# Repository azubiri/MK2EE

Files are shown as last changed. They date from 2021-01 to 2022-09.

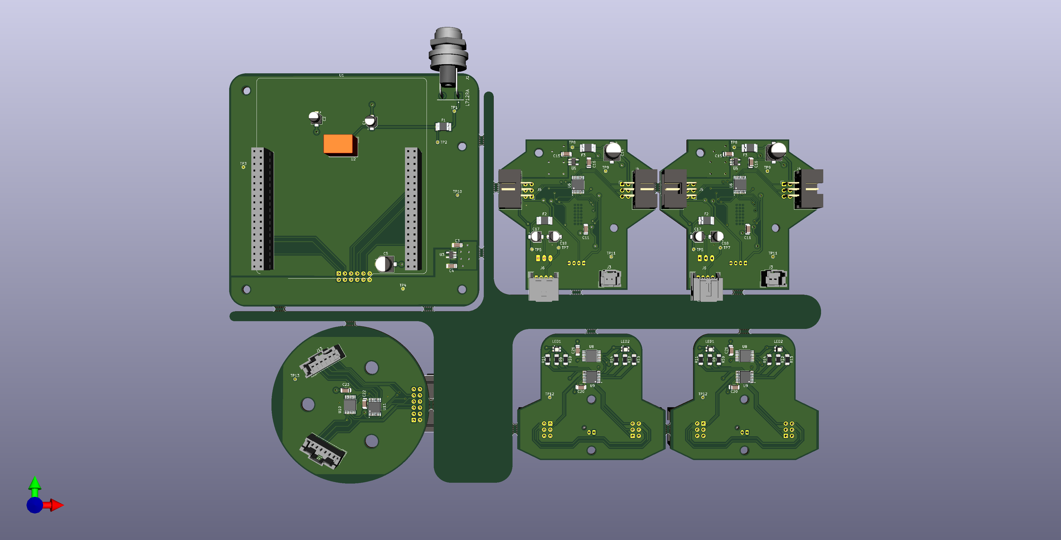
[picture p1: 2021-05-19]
mk2ee_kicad_project/Virtual_Images/PCBs_Manufactured_with_comp_front.png

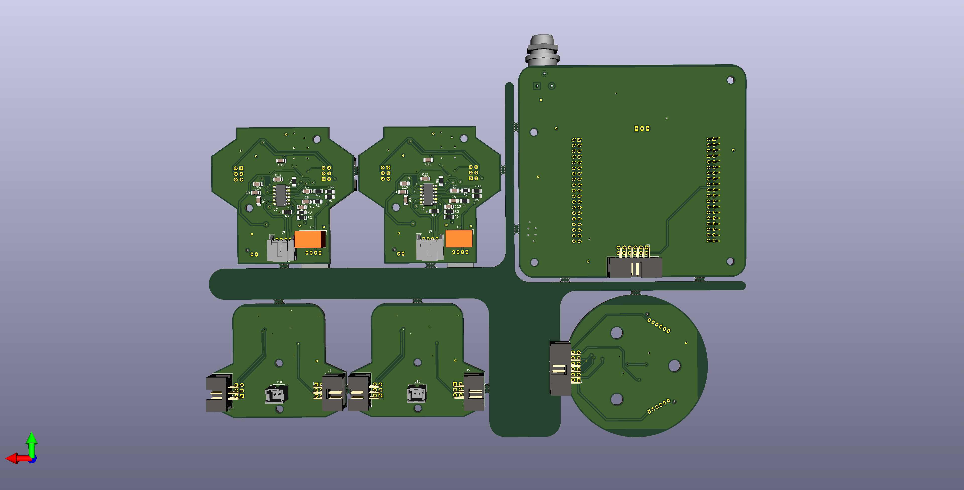
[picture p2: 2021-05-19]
mk2ee_kicad_project/Virtual_Images/PCBs_Manufactured_with_comp_back.png

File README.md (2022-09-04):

# MK2EE
## Introduction
The main goal of this project is a fabrication of robotic arm. This project is based on a previous project that is called [MK2Plus](https://www.instructables.com/Robot-Arm-MK2-Plus-Stepper-Motor-Used/). This previous project is a purpose which the joints of the robot are moved by stepper motors instead of servo motors like another project [EEZYbotARM MK2](http://www.eezyrobots.it/eba_mk2.html).

These additions which are implemented in this project are the following:
* Rotatory information of the joints that are provided by magnetic encoders.
* All electronic is integrated in the robot.
* Stressfuls for cables are avoided.

In this repository you will find the several files to replicate and improve this purposed robotic arm. It is structured by the mechanical part, electronic part and software that have been used to test the electronic part. In addition, there is anohter folder where you will find some software tools.

This project was a part of Master's Thesis. You can see more details about it in the documentation folder.

## Software requirements
### Mechanical part
* Autodesk Fusion 360 (recommended)
* FreeCAD (optional)
### Electronic part
* KiCad
### Software testing
* Visual Studio Code with PlatformIO extension (recommended)
* Mbed OS (optional)
### Software utilities
* Jupyter Notebook

## ToDo list
### Mechanical Part
- [ ] Paste one of the gear that is coupled with a stepper motor.
- [ ] Make a new gripper using a microservo and energised with 5V.

### Electronical Part
- [ ] Solder 2 EncoderPCB
- [ ] Solder 2 DriverPCB
- [ ] Solder 1 EncoderPCB2
- [ ] Solder 1 SupplyPCB

(see some important information in the README file inside mk2ee_kicad_project)

### Firmware Part
- [x] Test EncoderPCB with a Nucleo Board F303RE
- [x] Test DriverPCB with a Nucleo Board F303RE
- [x] Test EncoderPCB with a Nucleo Board F411RE
- [x] Test DriverPCB with a Nucleo Board F411RE
- [ ] Test EncoderPCB2 with a Nucleo Board F411RE
- [ ] Final testing SupplyPCB + EncoderPCB2 + 3xEncoderPCB + 3xDriverPCB

(see more details in the README file inside mk2ee_software_testing folder)

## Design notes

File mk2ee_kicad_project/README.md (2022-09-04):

# Electronical part
You can use these files to modify the circuits and PCBs with Kicad.

## Reworkings
- The linear regulator that is used in the DriverPCB design, is not found in the market. You can use other regulators with the same case style, but the function of each pin is different.
- The pads of the RGB leds in EncoderPCB. Pin 1 has to be put as cathode, and the rest (2, 3 and 4) as anode.

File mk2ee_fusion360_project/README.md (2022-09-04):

# Mechanical part
If you just want print the different parts of the robot, you can use directly the STL files.
But if you want to make modifications, you have to use the .f3z file using Fusion 360 software.

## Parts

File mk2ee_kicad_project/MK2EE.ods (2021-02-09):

Individual Components:
 |  | Reference(s) | Value | LibPart | Footprint | Manufacturer | Name
 |  | C1 | 10uF | Device:CP1 | Capacitor_SMD:CP_Elec_4x5.4 | Panasonic | EEEFK1E100R
 |  | C2 | 10uF | Device:CP1 | Capacitor_SMD:CP_Elec_4x5.4 | Kemet | EDK106M063A9GAA
 |  | C3 | 1uF | Device:C | Capacitor_SMD:C_1206_3216Metric | MULTICOMP PRO | MC1206B102K500CT
 |  | C4 | 1uF | Device:C | Capacitor_SMD:C_1206_3216Metric | MULTICOMP PRO | MC1206B102K500CT
 |  | C5 | 100uF | Device:CP1 | Capacitor_SMD:CP_Elec_6.3x7.7 | Panasonic | EEEFK1E101XP
 |  | C6 | 1000pF | Device:C | Capacitor_SMD:C_1206_3216Metric | MULTICOMP PRO | MC1206B102K500CT
 |  | C7 | 1000pF | Device:C | Capacitor_SMD:C_0805_2012Metric_Pad1.15x1.40mm_HandSolder | MULTICOMP PRO | MC1206B102K500CT
 |  | C8 | 0.22uF | Device:C | Capacitor_SMD:C_1206_3216Metric | Kemet | C1206C224K5RACTU
 |  | C9 | 0.22uF | Device:C | Capacitor_SMD:C_1206_3216Metric | Kemet | C1206C224K5RACTU
 |  | C10 | 0.22uF | Device:C | Capacitor_SMD:C_1206_3216Metric | Kemet | C1206C224K5RACTU
 |  | C11 | 100nF | Device:C | Capacitor_SMD:C_1206_3216Metric | Kemet | C1206C104K5RACTU
 |  | C12 | 100nF | Device:C | Capacitor_SMD:C_1206_3216Metric | Kemet | C1206C104K5RACTU
 |  | C13 | 100nF | Device:C | Capacitor_SMD:C_1206_3216Metric | Kemet | C1206C104K5RACTU
 |  | C14 | 100uF | Device:CP1 | Capacitor_SMD:CP_Elec_6.3x7.7 | Panasonic | EEEFK1E101XP
 |  | C15 | 1uF | Device:C | Capacitor_SMD:C_1206_3216Metric
 |  | C16 | 1uF | Device:C | Capacitor_SMD:C_1206_3216Metric
 |  | C17 | 10uF | Device:CP1 | Capacitor_SMD:CP_Elec_4x5.4 | Panasonic | EEEFK1E100R
 |  | C18 | 10uF | Device:CP1 | Capacitor_SMD:CP_Elec_4x5.4 | Panasonic | EEEFK1E100R
 |  | C19 | 100nF | Device:C | Capacitor_SMD:C_1206_3216Metric | Kemet | C1206C104K5RACTU
 |  | C20 | 100nF | Device:C
 |  | C21 | 100nF | Device:CP1 | Capacitor_SMD:CP_Elec_6.3x7.7 | Kemet | EDK106M063A9GAA
 |  | C22 | 100nF | Device:C
 |  | C23 | 100nF | Device:C
 |  | F1 | Polyfuse | MINISMDC110F_16-2:MINISMDC110F_16-2 | MK2Library:MINISMDC110 | Littlefuse | MINISMDC110F/24-2
 |  | F2 | Polyfuse | MINISMDC110F_16-2:MINISMDC110F_16-2 | MK2Library:MINISMDC110 | Littlefuse | MINISMDC110F/24-2
 |  | F3 | Polyfuse | MINISMDC110F_16-2:MINISMDC110F_16-2 | MK2Library:MINISMDC110 | Littlefuse | MINISMDC110F/24-2
 |  | J1 | L712RA | Switchcraft_-_L712RA:L712RA | MK2Library:Switchcraft-L712RA-0 | Switchcraft | L712RAS
 |  | J2 | Conn_02x6_Male | Connector:Conn_01x12_Male | Connector_PinSocket_2.54mm:PinSocket_2x06_P2.54mm_Horizontal | AMPHENOL ICC | T821112A1R100CEU
 |  | J3 | Conn_01x02_Male | Connector:Conn_01x02_Male | MK2Library:Molex_MicroClasp_55932-0210_1x02_P2.00mm_Vertical | Molex | 55932-0210
 |  | J4 | Conn_02x03_Male | Connector:Conn_01x06_Male | Connector_IDC:IDC-Header_2x03_P2.54mm_Horizontal | AMPHENOL ICC | T821106A1R100CEU
 |  | J5 | Conn_02x03_Male | Connector:Conn_01x06_Male | Connector_IDC:IDC-Header_2x03_P2.54mm_Horizontal | AMPHENOL ICC | T821106A1R100CEU
 |  | J6 | Conn_01x04_Male | Connector:Conn_01x04_Male | MK2Library:Molex_MicroClasp_55935-0430_1x04_P2.00mm_Horizontal | Molex | 502443-0470
 |  | J7 | Conn_01x04_Male | Connector:Conn_01x04_Male | MK2Library:Molex_MicroClasp_55935-0430_1x04_P2.00mm_Horizontal | Molex | 502443-0470
 |  | J8 | Conn_02x03_Male | Connector:Conn_01x06_Male | Connector_IDC:IDC-Header_2x03_P2.54mm_Horizontal | AMPHENOL ICC | T821106A1R100CEU
 |  | J9 | Conn_02x03_Male | Connector:Conn_01x06_Male | Connector_IDC:IDC-Header_2x03_P2.54mm_Horizontal | AMPHENOL ICC | T821106A1R100CEU
 |  | J10 | Conn_01x02_Male | Connector:Conn_01x02_Male | MK2Library:Molex_MicroClasp_55932-0210_1x02_P2.00mm_Vertical | Molex | 55932-0210
 |  | J11 | Conn_02x6_Male | Connector:Conn_01x12_Male | Connector_PinSocket_2.54mm:PinSocket_2x06_P2.54mm_Horizontal | AMPHENOL ICC | T821112A1R100CEU
 |  | J12 | Conn_02x03_Male | Connector:Conn_01x06_Male | MK2Library:901303206 | Molex | 90130-3206
 |  | J13 | Conn_02x03_Male | Connector:Conn_01x06_Male | MK2Library:901303206 | Molex | 90130-3206
 |  | LED1 | ASMB-KTF0-0A306 | ASMB-KTF0-0A306:ASMB-KTF0-0A306 | MK2Library:ASMBKTF00A306 | Avago Technologies | ASMB-KTF0-0A306
 |  | LED2 | ASMB-KTF0-0A306 | ASMB-KTF0-0A306:ASMB-KTF0-0A306 | MK2Library:ASMBKTF00A306 | Avago Technologies | ASMB-KTF0-0A306
 |  | R1 | 47k | Device:R | Resistor_SMD:R_1206_3216Metric | MULTICOMP PRO | MCWR12X4702FTL
 |  | R2 | 10k | Device:R | Resistor_SMD:R_0805_2012Metric_Pad1.15x1.40mm_HandSolder | MULTICOMP PRO | MC0125W1206510K
 |  | R3 | 10k | Device:R | Resistor_SMD:R_0805_2012Metric_Pad1.15x1.40mm_HandSolder | MULTICOMP PRO | MC0125W1206510K
 |  | R4 | 10k | Device:R | Resistor_SMD:R_0805_2012Metric_Pad1.15x1.40mm_HandSolder | MULTICOMP PRO | MC0125W1206510K
 |  | R5 | 10k | Device:R | Resistor_SMD:R_0805_2012Metric_Pad1.15x1.40mm_HandSolder | MULTICOMP PRO | MC0125W1206510K
 |  | R6 | 47k | Device:R | Resistor_SMD:R_1206_3216Metric | MULTICOMP PRO | MCWR12X4702FTL
 |  | R7 | 0.43R | Device:R | Resistor_SMD:R_1206_3216Metric | BOURNS | CRL1206-FW-R430ELF
 |  | R8 | 0.43R | Device:R | Resistor_SMD:R_0805_2012Metric_Pad1.15x1.40mm_HandSolder | BOURNS | CRL1206-FW-R430ELF
 |  | R9 | 82 | Device:R | Resistor_SMD:R_1206_3216Metric | MULTICOMP PRO | MCWR12X82R0FTL
 |  | R10 | 100 | Device:R | Resistor_SMD:R_1206_3216Metric | MULTICOMP PRO | MCWR12X1000FTL
 |  | R11 | 270 | Device:R | Resistor_SMD:R_1206_3216Metric | MULTICOMP PRO | MCWR12X2700FTL
 |  | R12 | 82 | Device:R | Resistor_SMD:R_1206_3216Metric | MULTICOMP PRO | MCWR12X82R0FTL
 |  | R13 | 100 | Device:R | Resistor_SMD:R_1206_3216Metric | MULTICOMP PRO | MCWR12X1000FTL
 |  | R14 | 270 | Device:R | Resistor_SMD:R_1206_3216Metric | MULTICOMP PRO | MCWR12X2700FTL
 |  | U1 | NUCLEO-F411RE | NUCLEO-F411RE:NUCLEO-F401RE | MK2Library:ST_NUCLEO-F401RE | STMicroelectronics | Nucleo-F411RE
 |  | U2 | TSR_1-24150 | Regulator_Switching:TSR_1-24150 | Converter_DCDC:Converter_DCDC_TRACO_TSR-1_THT | Traco Power | TSR 1-2450
 |  | U3 | NCP718xSN330 | Regulator_Linear:NCP718xSN330 | Package_TO_SOT_SMD:SOT-23-5 | ON SEMICONDUCTOR | NCP718BSN330T1G
 |  | U4 | TSR_1-2465 | Regulator_Switching:TSR_1-2465 | Converter_DCDC:Converter_DCDC_TRACO_TSR-1_THT | Traco Power | TSR 2-2465
 |  | U5 | NCP718xSN330 | Regulator_Linear:NCP718xSN330 | Package_TO_SOT_SMD:SOT-23-5
 |  | U6 | 74HC595 | 74xx:74HC595 | MK2Library:SN74HC595PWR | Texas Instruments | SN74HC595PWR
 |  | U7 | DRV8818PWP | DRV8818PWP:DRV8818PWP | MK2Library:DRV8818PWP | Texas Instruments | DRV8818PWR
 |  | U8 | AS5047D-ATSM | AS5047D-ATSM:AS5047D-ATSM | MK2Library:AS5047D-ATSM | ams | AS5047D-ATSM
 |  | U9 | 74HC595 | 74xx:74HC595 | MK2Library:SN74HC595PWR | Texas Instruments | SN74HC595PWR
 |  | U10 | AS5047D-ATSM | AS5047D-ATSM:AS5047D-ATSM | MK2Library:AS5047D-ATSM | ams | AS5047D-ATSM
 |  | U11 | 74HC595 | 74xx:74HC595 | MK2Library:SN74HC595PWR | Texas Instruments | SN74HC595PWR
Collated Components:
Item | Qty | Reference(s) | Value | LibPart | Footprint | Manufacturer | Name
1 | 4 | C1, C2, C17, C18 | 10uF | Device:CP1 | Capacitor_SMD:CP_Elec_4x5.4 | Panasonic | EEEFK1E100R
2 | 4 | C3, C4, C15, C16 | 1uF | Device:C | Capacitor_SMD:C_1206_3216Metric | MULTICOMP PRO | MC1206B102K500CT
3 | 2 | C5, C14 | 100uF | Device:CP1 | Capacitor_SMD:CP_Elec_6.3x7.7 | Panasonic | EEEFK1E101XP
4 | 1 | C6 | 1000pF | Device:C | Capacitor_SMD:C_1206_3216Metric | MULTICOMP PRO | MC1206B102K500CT
5 | 1 | C7 | 1000pF | Device:C | Capacitor_SMD:C_0805_2012Metric_Pad1.15x1.40mm_HandSolder | MULTICOMP PRO | MC1206B102K500CT
6 | 3 | C8, C9, C10 | 0.22uF | Device:C | Capacitor_SMD:C_1206_3216Metric | Kemet | C1206C224K5RACTU
7 | 4 | C11, C12, C13, C19 | 100nF | Device:C | Capacitor_SMD:C_1206_3216Metric | Kemet | C1206C104K5RACTU
8 | 3 | C20, C22, C23 | 100nF | Device:C | Capacitor_SMD:C_1206_3216Metric | Kemet | C1206C104K5RACTU
9 | 1 | C21 | 100nF | Device:CP1 | Capacitor_SMD:CP_Elec_6.3x7.7 | Kemet | EDK106M063A9GAA
10 | 3 | F1, F2, F3 | Polyfuse | MINISMDC110F_16-2:MINISMDC110F_16-2 | MK2Library:MINISMDC110 | Littlefuse | MINISMDC110F/24-2
11 | 1 | J1 | L712RA | Switchcraft_-_L712RA:L712RA | MK2Library:Switchcraft-L712RA-0 | Switchcraft | L712RAS
12 | 2 | J2, J11 | Conn_02x6_Male | Connector:Conn_01x12_Male | Connector_PinSocket_2.54mm:PinSocket_2x06_P2.54mm_Horizontal | AMPHENOL ICC | T821112A1R100CEU
13 | 2 | J3, J10 | Conn_01x02_Male | Connector:Conn_01x02_Male | MK2Library:Molex_MicroClasp_55932-0210_1x02_P2.00mm_Vertical | Molex | 55932-0210
14 | 4 | J4, J5, J8, J9 | Conn_02x03_Male | Connector:Conn_01x06_Male | Connector_IDC:IDC-Header_2x03_P2.54mm_Horizontal | AMPHENOL ICC | T821106A1R100CEU
15 | 2 | J6, J7 | Conn_01x04_Male | Connector:Conn_01x04_Male | MK2Library:Molex_MicroClasp_55935-0430_1x04_P2.00mm_Horizontal | Molex | 502443-0470
16 | 2 | J12, J13 | Conn_02x03_Male | Connector:Conn_01x06_Male | MK2Library:901303206 | Molex | 90130-3206
17 | 2 | LED1, LED2 | ASMB-KTF0-0A306 | ASMB-KTF0-0A306:ASMB-KTF0-0A306 | MK2Library:ASMBKTF00A306 | Avago Technologies | ASMB-KTF0-0A306
18 | 2 | R1, R6 | 47k | Device:R | Resistor_SMD:R_1206_3216Metric | MULTICOMP PRO | MCWR12X4702FTL
19 | 4 | R2, R3, R4, R5 | 10k | Device:R | Resistor_SMD:R_0805_2012Metric_Pad1.15x1.40mm_HandSolder | MULTICOMP PRO | MC0125W1206510K
20 | 1 | R7 | 0.43R | Device:R | Resistor_SMD:R_1206_3216Metric | BOURNS | CRL1206-FW-R430ELF
21 | 1 | R8 | 0.43R | Device:R | Resistor_SMD:R_0805_2012Metric_Pad1.15x1.40mm_HandSolder | BOURNS | CRL1206-FW-R430ELF
22 | 2 | R9, R12 | 82 | Device:R | Resistor_SMD:R_1206_3216Metric | MULTICOMP PRO | MCWR12X82R0FTL
23 | 2 | R10, R13 | 100 | Device:R | Resistor_SMD:R_1206_3216Metric | MULTICOMP PRO | MCWR12X1000FTL
24 | 2 | R11, R14 | 270 | Device:R | Resistor_SMD:R_1206_3216Metric | MULTICOMP PRO | MCWR12X2700FTL
25 | 1 | U1 | NUCLEO-F411RE | NUCLEO-F411RE:NUCLEO-F401RE | MK2Library:ST_NUCLEO-F401RE | STMicroelectronics | Nucleo-F411RE
26 | 1 | U2 | TSR_1-24150 | Regulator_Switching:TSR_1-24150 | Converter_DCDC:Converter_DCDC_TRACO_TSR-1_THT | Traco Power | TSR 1-2450
27 | 2 | U3, U5 | NCP718xSN330 | Regulator_Linear:NCP718xSN330 | Package_TO_SOT_SMD:SOT-23-5 | ON SEMICONDUCTOR | NCP718BSN330T1G
28 | 1 | U4 | TSR_1-2465 | Regulator_Switching:TSR_1-2465 | Converter_DCDC:Converter_DCDC_TRACO_TSR-1_THT | Traco Power | TSR 2-2465
29 | 3 | U6, U9, U11 | 74HC595 | 74xx:74HC595 | MK2Library:SN74HC595PWR | Texas Instruments | SN74HC595PWR
30 | 1 | U7 | DRV8818PWP | DRV8818PWP:DRV8818PWP | MK2Library:DRV8818PWP | Texas Instruments | DRV8818PWR
31 | 2 | U8, U10 | AS5047D-ATSM | AS5047D-ATSM:AS5047D-ATSM | MK2Library:AS5047D-ATSM | ams | AS5047D-ATSM

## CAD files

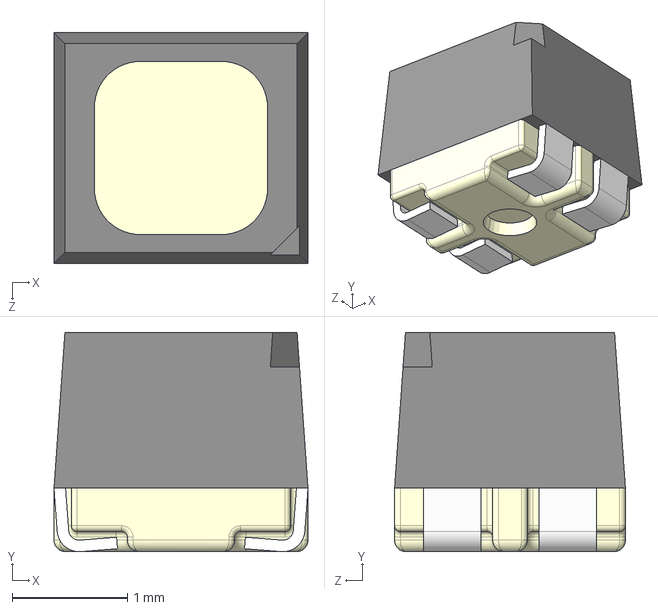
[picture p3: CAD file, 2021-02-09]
mk2ee_kicad_project/MK2Library/ASMB-KTF0-0A306.STEP
2.20 x 1.90 x 2.00 mm

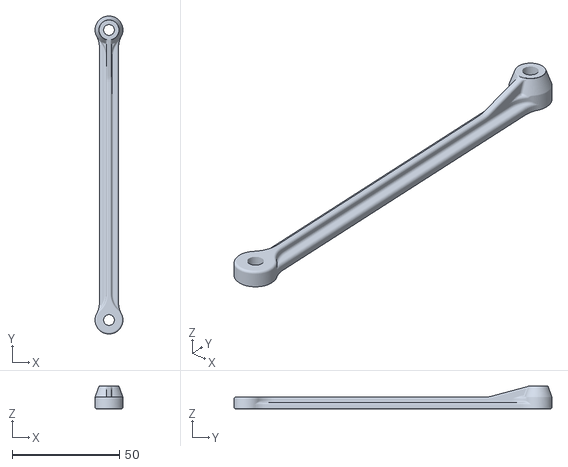
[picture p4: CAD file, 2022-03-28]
mk2ee_fusion360_project/stl_files/ShoulderLeftPart.stl
13.0 x 148.0 x 10.5

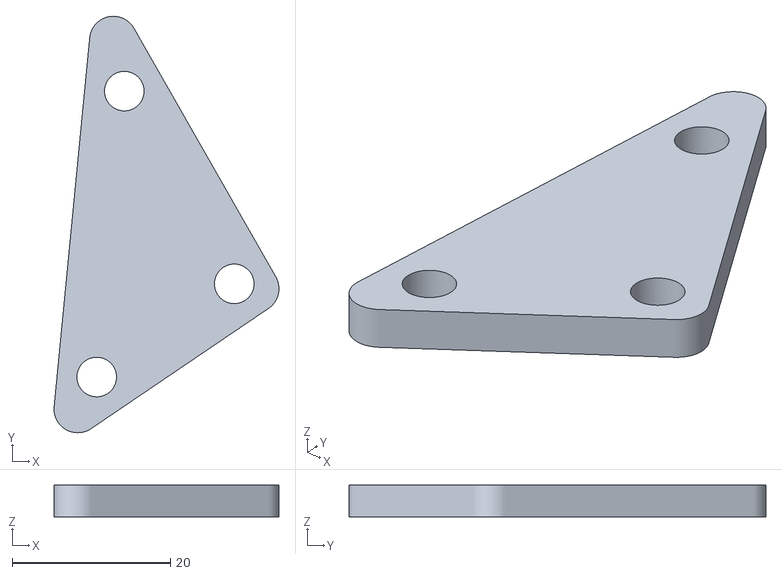
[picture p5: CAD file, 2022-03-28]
mk2ee_fusion360_project/stl_files/Aux Support.stl
28.4 x 52.6 x 4.00

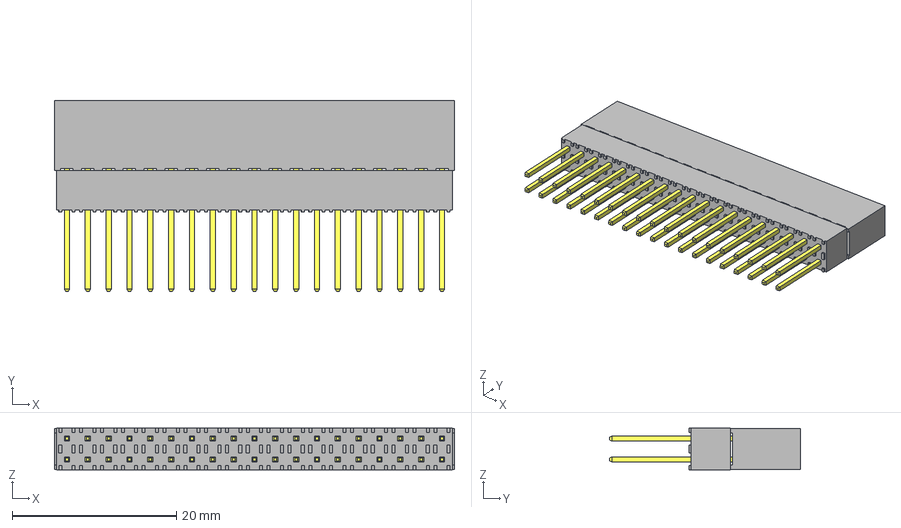
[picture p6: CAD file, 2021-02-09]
mk2ee_kicad_project/MK2Library/NUCLEO_ESQ-119-24-T-D.stp
48.8 x 23.2 x 5.08 mm
_ESQ-119-24-T-D_socket
_ESQ-119-24-T-D_pins
_ESQ-119-24-G-D-LL_bpins

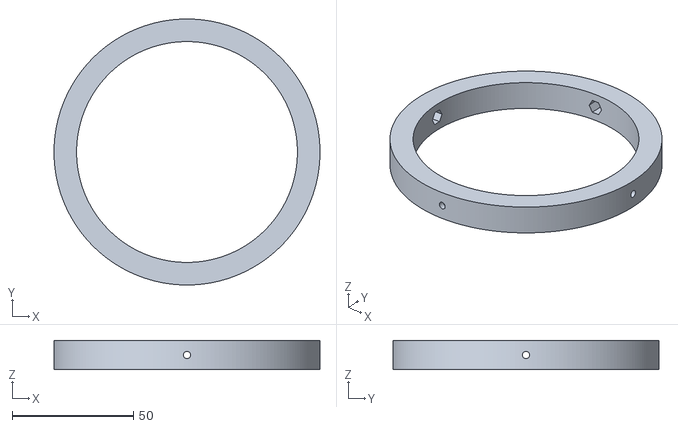
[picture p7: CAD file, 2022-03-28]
mk2ee_fusion360_project/stl_files/Vertical_TopLimit.stl
109.5 x 109.5 x 12.0

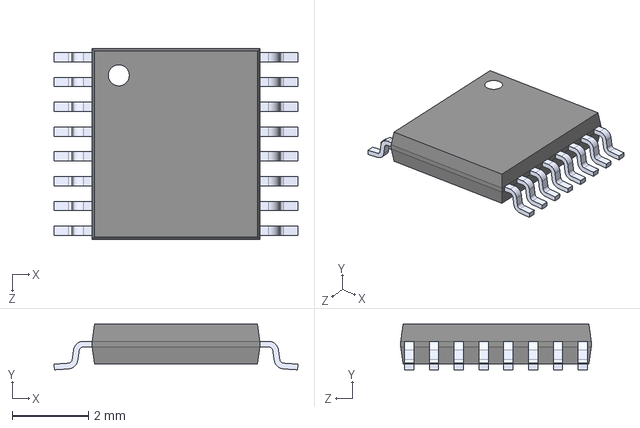
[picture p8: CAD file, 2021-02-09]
mk2ee_kicad_project/MK2Library/SN74HC595PWR.step
6.40 x 1.20 x 5.00 mm

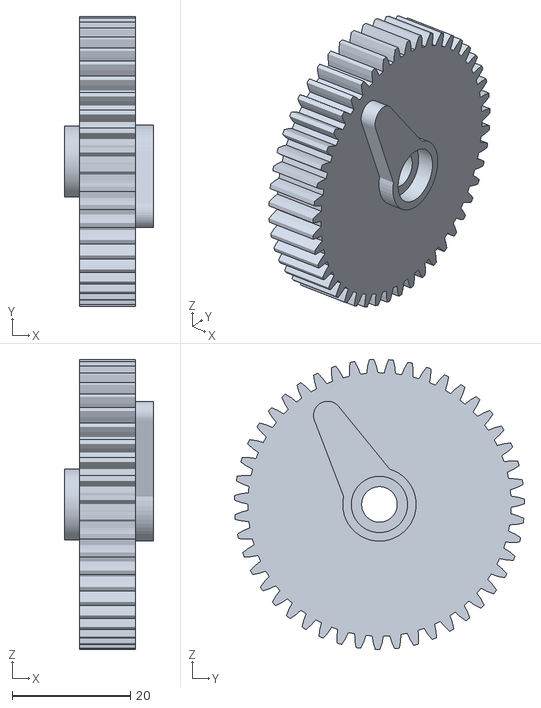
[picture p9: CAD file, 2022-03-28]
mk2ee_fusion360_project/stl_files/GearWithCouplerLeft.stl
15.0 x 49.0 x 49.0

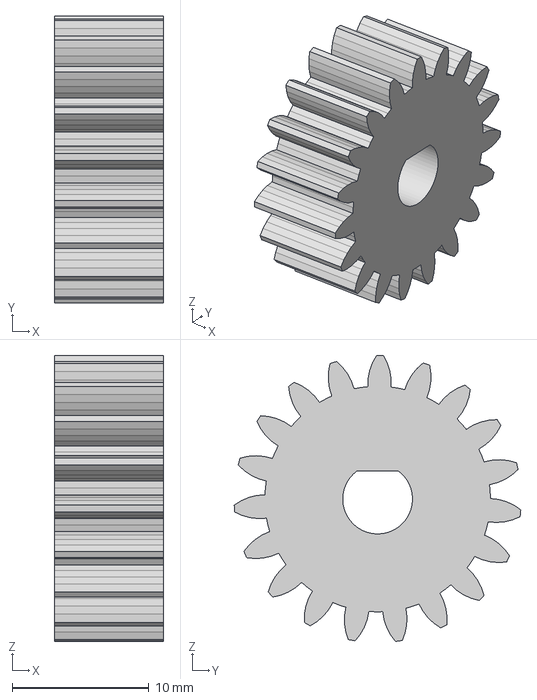
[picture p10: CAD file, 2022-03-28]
mk2ee_fusion360_project/stl_files/Gear_19z.step
8.00 x 21.0 x 20.9 mm

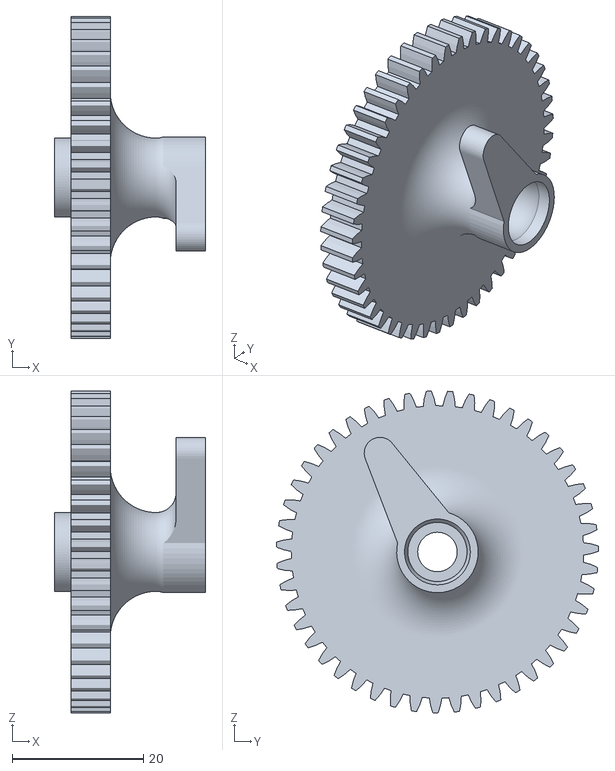
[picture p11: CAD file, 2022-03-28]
mk2ee_fusion360_project/stl_files/GearWithCouplerRight.stl
23.0 x 49.0 x 49.0

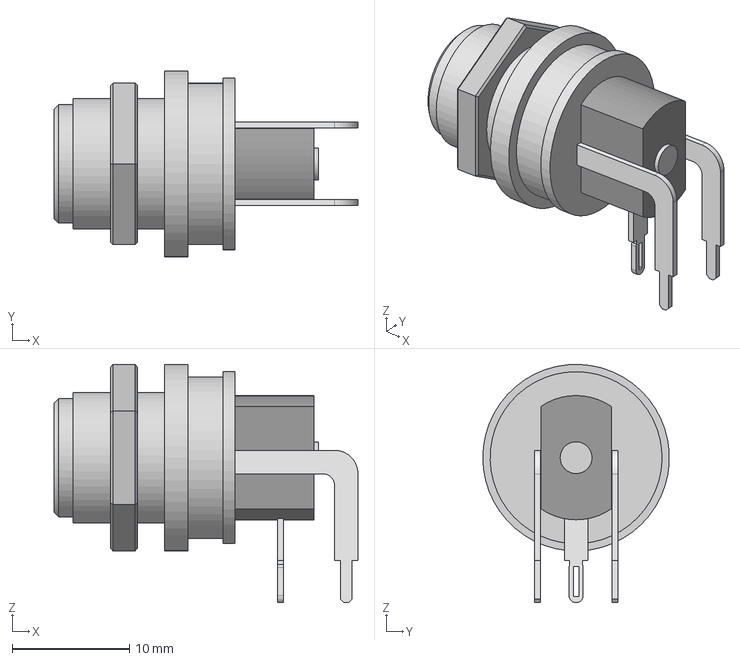
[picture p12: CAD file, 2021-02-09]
mk2ee_kicad_project/MK2Library/Switchcraft_-_L712RA.step
25.9 x 15.9 x 20.3 mm

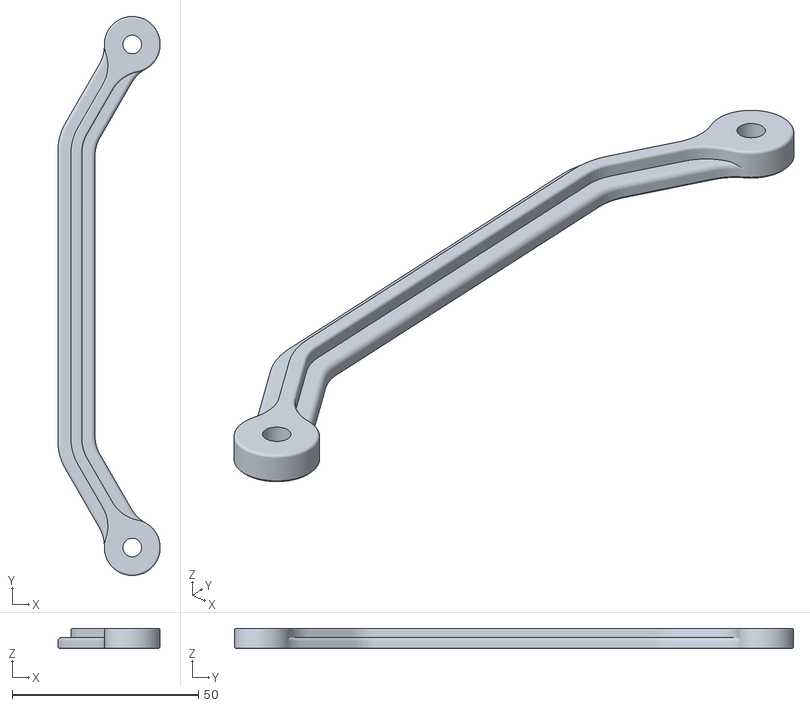
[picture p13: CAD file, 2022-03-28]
mk2ee_fusion360_project/stl_files/ShoulderRightPart.stl
27.5 x 150.0 x 5.50

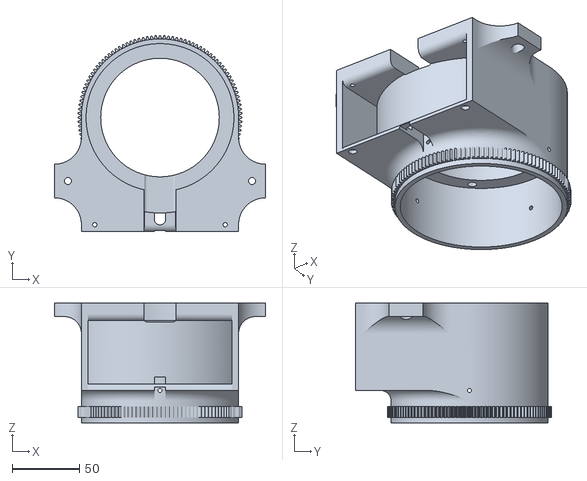
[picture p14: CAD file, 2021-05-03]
mk2ee_fusion360_project/stl_files/BaseGearCover.stl
157.0 x 145.7 x 89.0

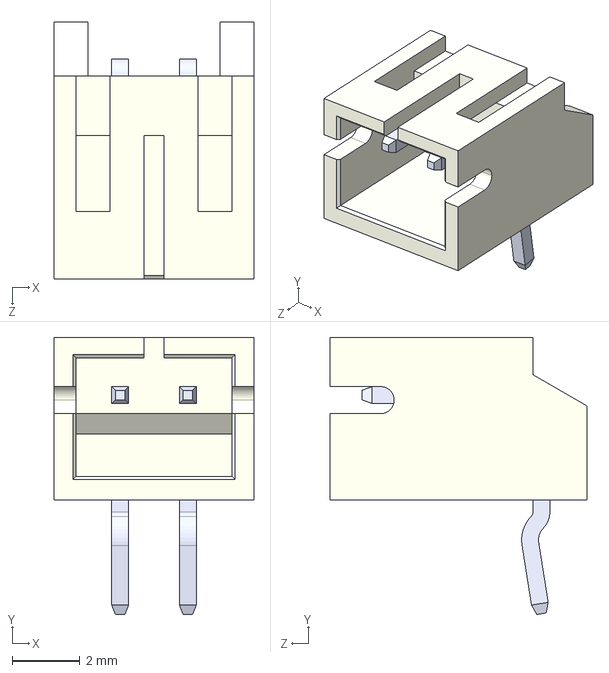
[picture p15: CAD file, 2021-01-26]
mk2ee_kicad_project/MK2Library/S2B-PH-K-S_LF__SN_.STEP
5.90 x 8.18 x 7.60 mm

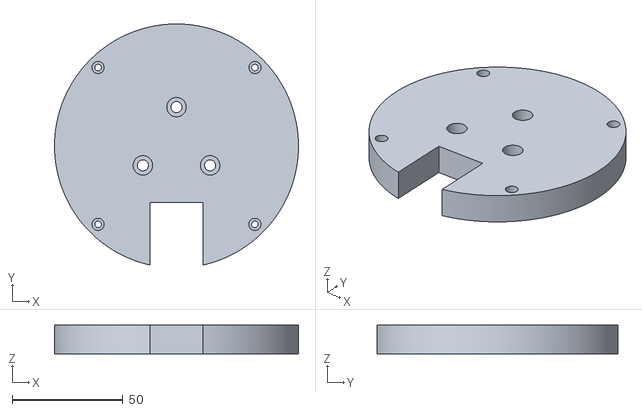
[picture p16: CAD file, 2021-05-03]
mk2ee_fusion360_project/stl_files/BaseGearButtom.stl
110.0 x 108.7 x 13.0

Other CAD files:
mk2ee_fusion360_project/stl_files/Gear_19zv5.stl
mk2ee_kicad_project/MK2Library/DRV8825PWPR--3DModel-STEP-56544.STEP
mk2ee_fusion360_project/stl_files/MotorBasePlatform_Body.stl
mk2ee_kicad_project/MK2Library/AS5047D-ATSM.stp
mk2ee_fusion360_project/MK2 Encoder Enhaced v79.f3z
mk2ee_fusion360_project/stl_files/Ball_Bearing_Separator v1.stl
mk2ee_fusion360_project/stl_files/BaseGear.stl
mk2ee_fusion360_project/stl_files/BaseGearBox.stl
mk2ee_fusion360_project/stl_files/BaseServo.stl
mk2ee_fusion360_project/stl_files/Bottom_platform_mobile.stl
mk2ee_fusion360_project/stl_files/ElbowRightPart.stl
mk2ee_fusion360_project/stl_files/GearWithCoupler.stl
mk2ee_fusion360_project/stl_files/Gear_19z v4.stl
mk2ee_fusion360_project/stl_files/Gear_19z.stl
mk2ee_fusion360_project/stl_files/Gear_24z.stl
mk2ee_fusion360_project/stl_files/Hold Shoulder.stl
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

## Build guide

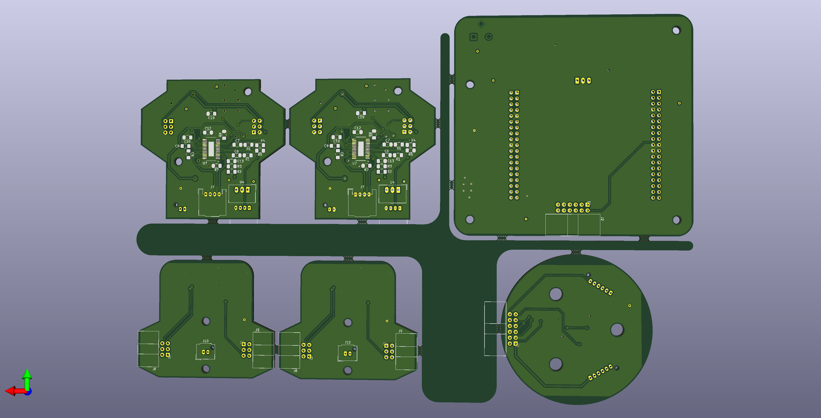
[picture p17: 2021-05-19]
mk2ee_kicad_project/Virtual_Images/PCBs_Manufactured_without_comp_back.png

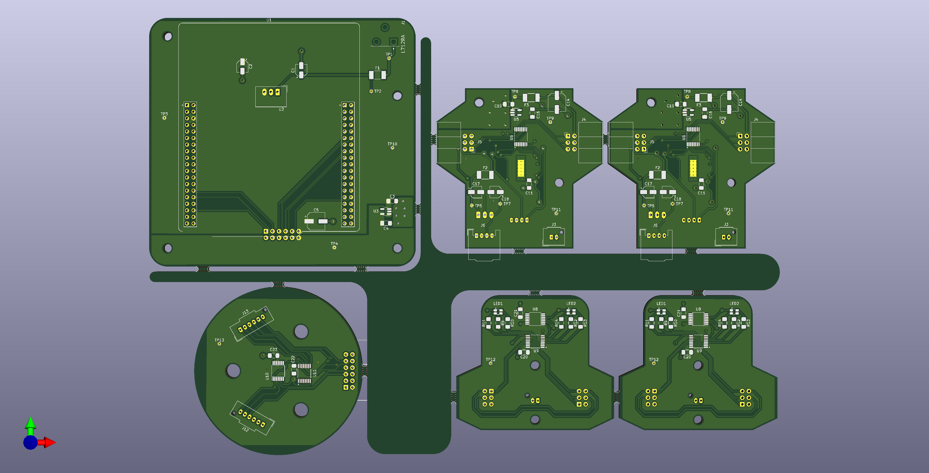
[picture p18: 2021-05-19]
mk2ee_kicad_project/Files_to_manufacturer/PCBs_Manufactured_without_comp_front.png

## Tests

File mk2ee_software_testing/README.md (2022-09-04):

# Software Testing
Every single folder is a independent project to test the hardware.

## AS5047D_SPI_Two
### Summary
It tests a reading of two magnetic encoders via a SPI communication. It doesn't test a EncoderPCB.
### Hardware required
- 2 x AS5047D (magnetic encoder)
- 2 x Capacitor (100nF)
- 2 x Magnets with a radial magnetization
- 1 x Nucleo Board

## DRV8818 (deprecated)
### Summary
It tests a DriverPCB which it is communicated with a Nucleo Board via SPI.
It uses arithmetic operators, that's why this code is deprecated.
### Hardware required
- 1 x DriverPCB
- 1 x Nucleo Board

## DRV8818_AS5047D_SPI (deprecated)
### Summary
It tests a DriverPCB and an EncoderPCB that they are communicated with a Nucleo Board via two different SPI peripherals.
It uses arithmetic operators, that's why this code is deprecated.
### Hardware required
- 1 x DriverPCB
- 1 x EncoderPCB
- 1 x Magnet with radial magnetization
- 1 x Nucleo Board

## EncoderPCB (deprecated)
### Summary
It tests an EncoderPCB setting up SPI registers directly from a Nucleo Board F411RE.
### Hardawre required
- 1 x EncoderPCB
- 1 x Magnet with radial magnetization
- 1 x Nucleo Board F411RE

## EncoderPCB_303
### Summary
It tests an EncoderPCB setting up SPI registers directly from a Nucleo Board F303RE.
Every module is coded for each digital electronic component.

Recomendations:
- I recommend to continue this code in order to finish the project.
- You can use the SPI settings that they are inside "EncoderPCB" folder in order to use a F303RE board.
- You add a module to programm the driver. Use the interface made here.

###Hardware required
- 1 x EncoderPCB
- 1 x Magnet with radial magnetization
- 1 x Nucleo Board F411RE

## Servo_PWM (deprecated)
### Summary
It tests the servo motor which is connected with a Nucleo Board, and it's controlled via PWM.
### Hardware Required
- 1 x Servo MG996
- 1 x Nucleo board (F411RE or F303RE)

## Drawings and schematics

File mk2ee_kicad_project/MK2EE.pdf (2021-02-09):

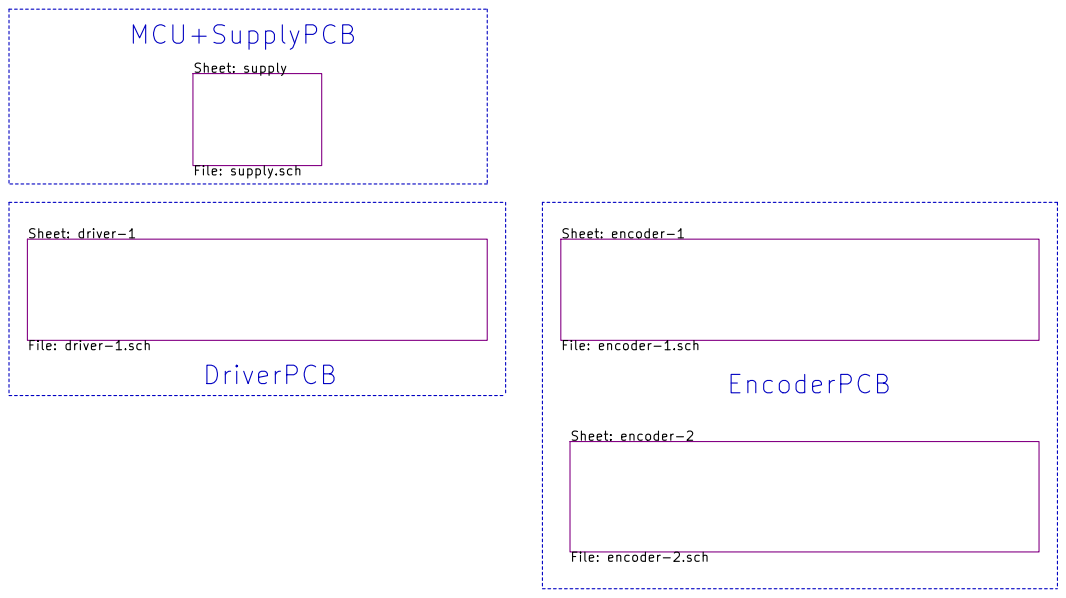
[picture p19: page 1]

File: MK2EE.sch Sheet: / ETSETB/UPC

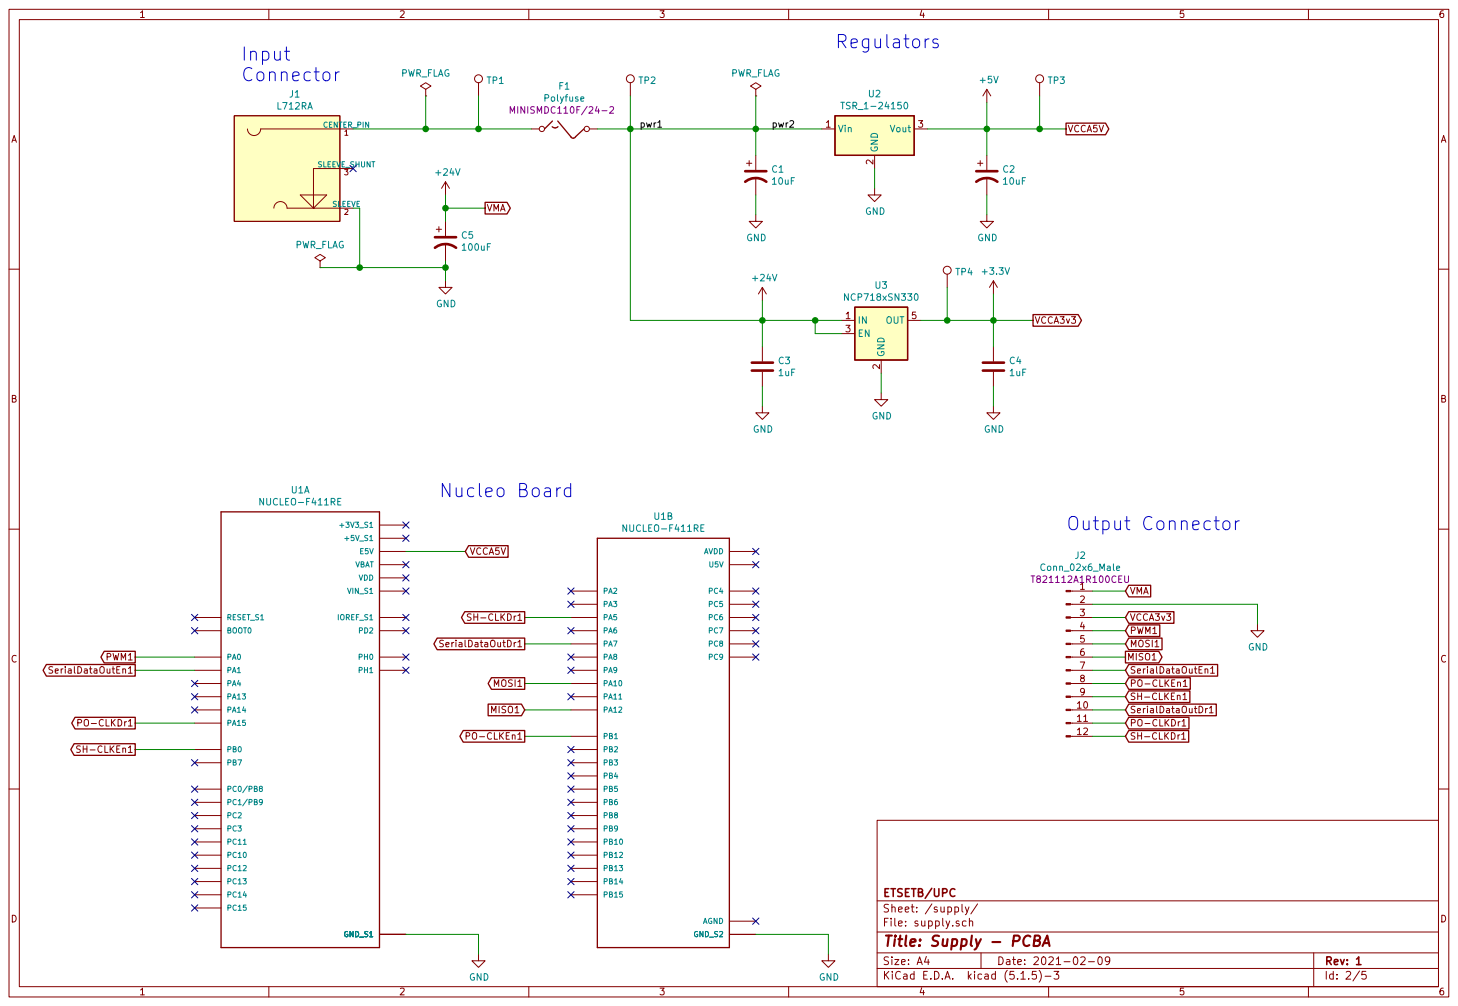
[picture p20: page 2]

Sheet: /supply/ ETSETB/UPC

File: supply.sch
Id: 2/5 Title: Supply - PCBA

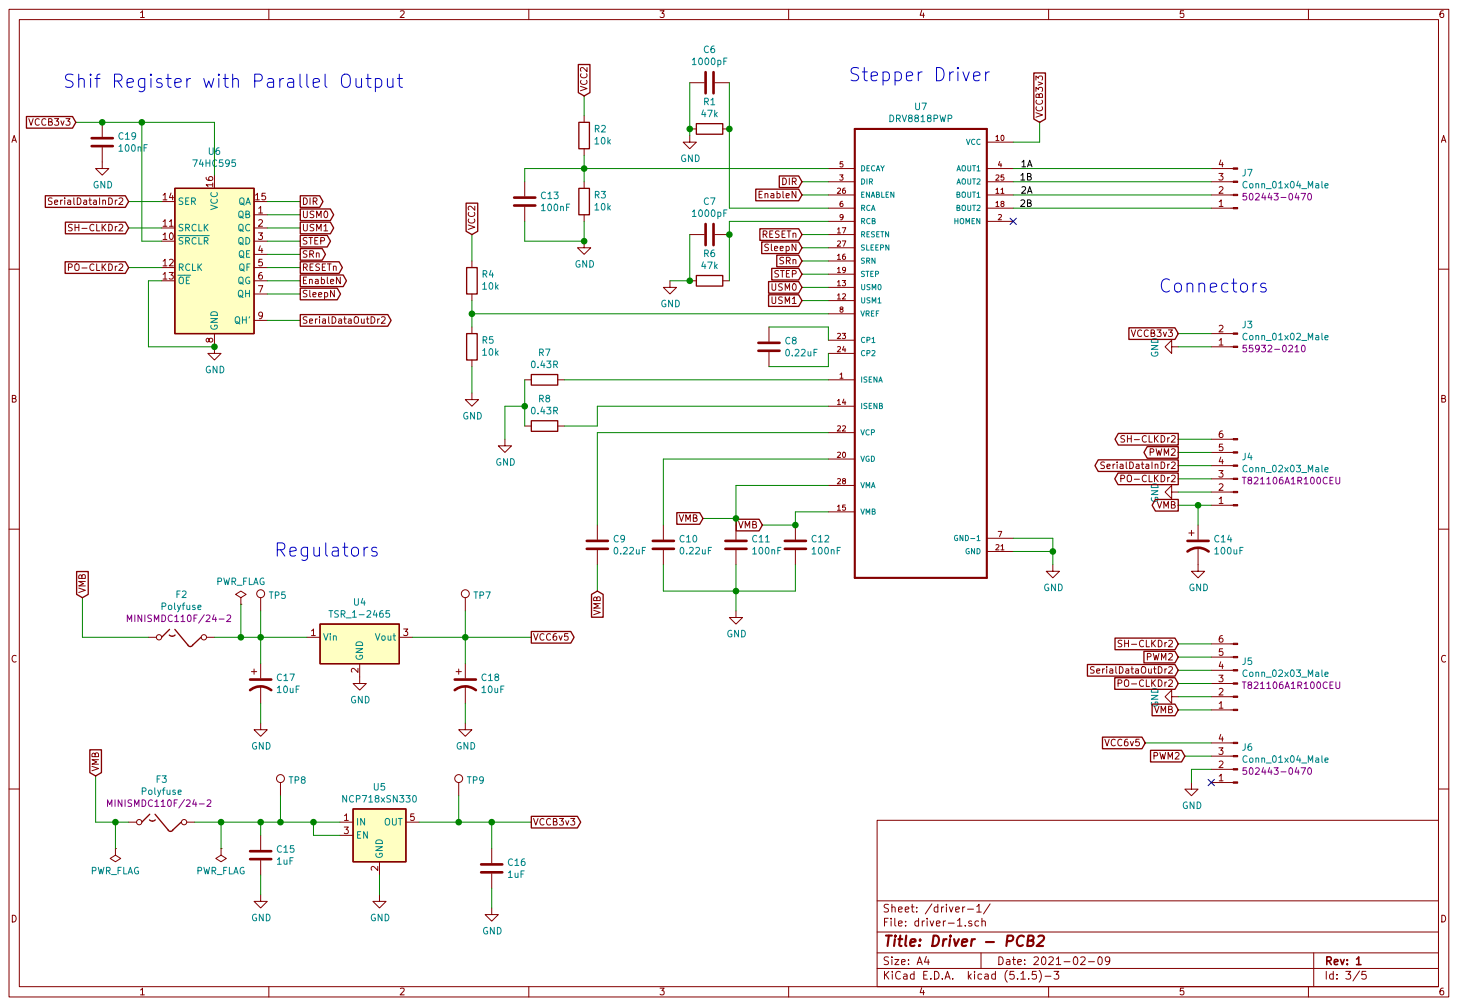
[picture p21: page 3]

File: driver-1.sch Sheet: /driver-1/ GND

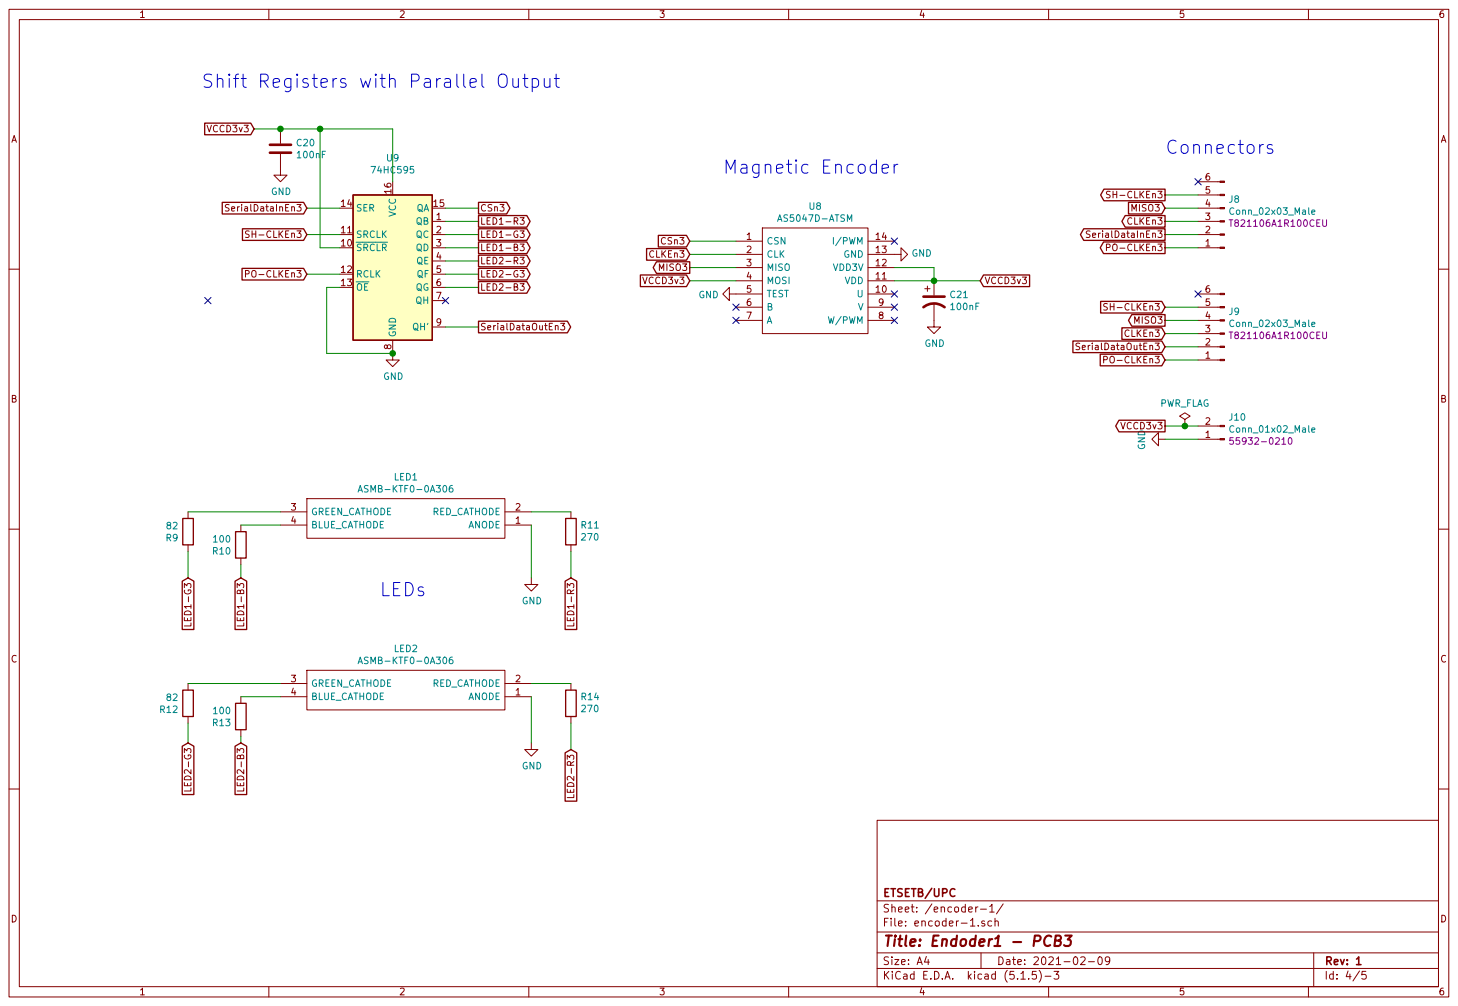
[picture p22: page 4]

Shift Registers with Parallel Output

File: encoder-1.sch Sheet: /encoder-1/ ETSETB/UPC

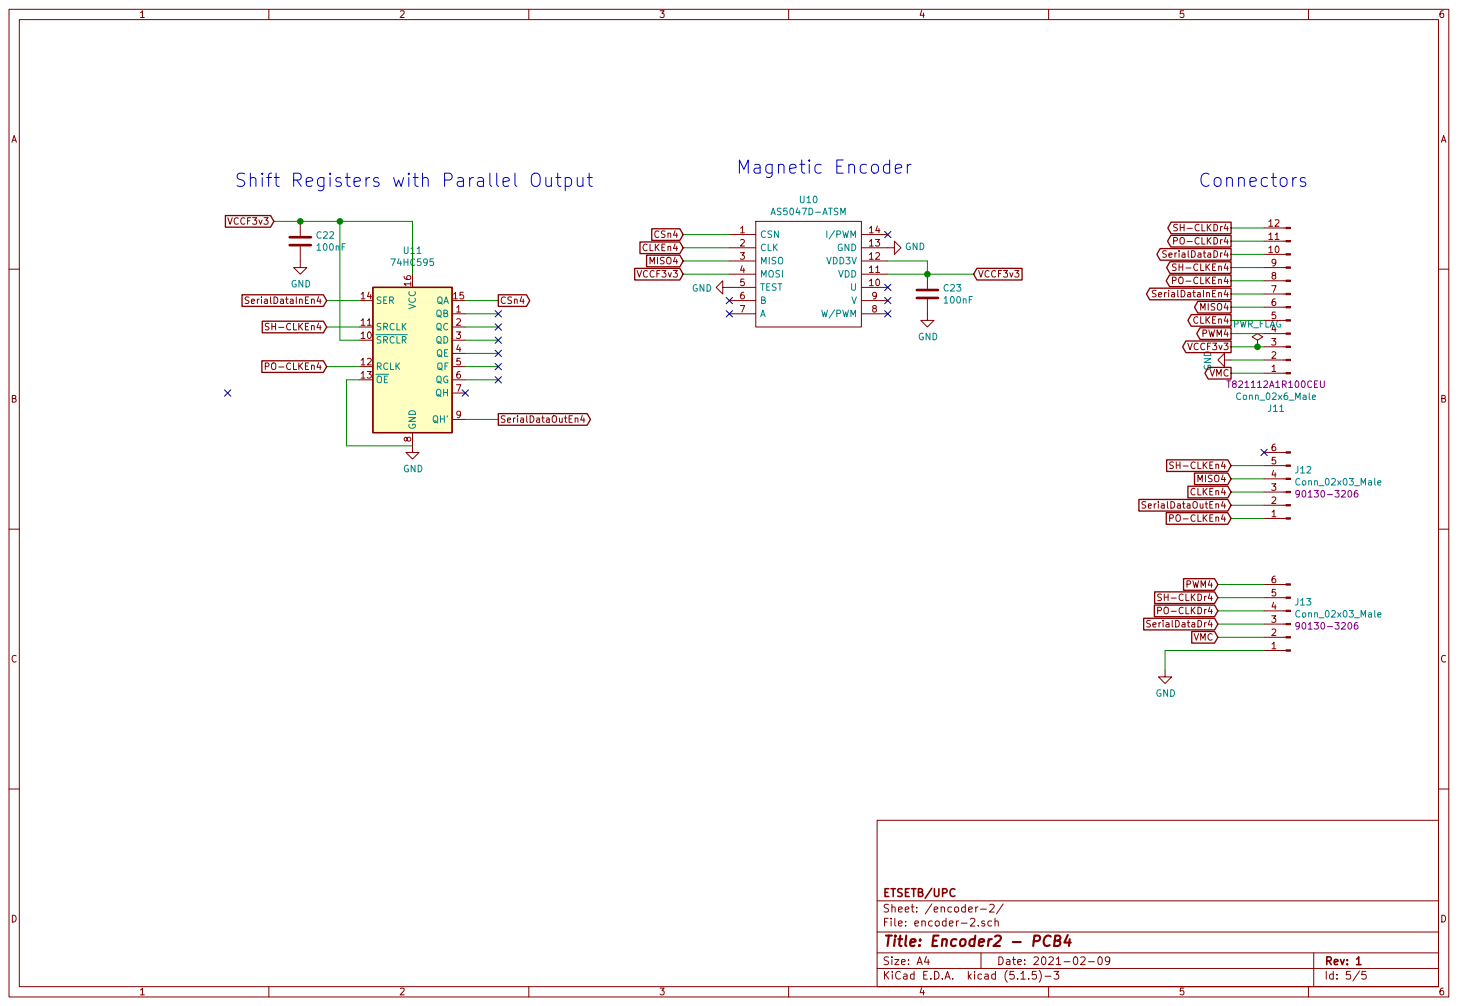
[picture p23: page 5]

File: encoder-2.sch Sheet: /encoder-2/ ETSETB/UPC

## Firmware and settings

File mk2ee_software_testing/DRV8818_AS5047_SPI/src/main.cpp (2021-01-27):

#include <mbed.h>
#include <cmath>

#define PULSE_DURATION 25 // Pulse duration SRCLK or RCLK high or low (in nanoseconds) 

typedef enum {
    AS_FLAG_PARITY = 0x8000,
    AS_FLAG_READ = 0x4000,
} As5047Flag;

typedef enum {
    AS_CMD_NOP = 0x0000,
    AS_CMD_ERROR = 0x0001 | AS_FLAG_READ,       // Reads error register of sensor and clear error flags
    AS_CMD_DIAGNOSTICS = 0x3FFD |  AS_FLAG_READ, // Reads automatic gain control and diagnostics info
    AS_CMD_MAGNITUDE = 0x3FFE | AS_FLAG_READ,
    
    AS_CMD_ANGLE = 0x3FFF| AS_FLAG_PARITY | AS_FLAG_READ,
} As5047Command;

// Masks for bits in the result of the AS_CMD_DIAGNOSTICS command
typedef enum {
    AS_DIAG_CORDIC_OVERFLOW = 0x0200,
    AS_DIAG_HIGH_MAGNETIC = 0x0400,
    AS_DIAG_LOW_MAGNETIC = 0x0800,
} As5047Diagnostics;

SPI encoder(PA_7, PA_6, PA_5);

SPI shPo(PC_12, PC_11, PC_10);
DigitalOut csn_shpo(A3, 1);
// Shift Register transmitter and receiver
uint16_t data_tx;
uint16_t data_rx;

static Serial pc(USBTX, USBRX, 115200); // tx, rx

// Parallel outputs
// Driver parameters
uint8_t stepper_dir, stepper_usm1, stepper_usm0, 
    stepper_sleepn, stepper_step, stepper_resetn, 
    stepper_srn, stepper_enablen;
// Encoder parameter
uint8_t csn_encoder;

int velocity = 10000; // 10 ms

// Shift Register Code ////////////
void latchSignal() {
    csn_shpo = 1;
    wait_ns(PULSE_DURATION);
    csn_shpo = 0;
}

void shiftOut(uint16_t data_tx, uint16_t *data_rx ) {
    *data_rx = shPo.write(data_tx);
    latchSignal();
}
//////////////////////////////////

// Encoder Code //////////////////
int mask(int sensor_result)
{
    return sensor_result & 0x3FFF; // return lowest 14-bits
}

float degrees(int sensor_result)
{
    float conversor, angle;
    conversor = 360.0 / 16384.0;
    // pc.printf("Conv: %f\n", conversor);
    angle = mask(sensor_result);
    // pc.printf("Angle in 14 bits: %f\n", angle);
    return angle * conversor;
}

bool parity_check(int sensor_result)
{
    // Use the LSb of result to keep track of parity (0 = even, 1 = odd)
    int result = sensor_result;
    
    for(int i = 1; i <= 15; ++i) {
        sensor_result >>= 1;
        // pc.printf("Sensor result: 0x%04X\n", sensor_result);
        result ^= sensor_result;
        // pc.printf("Result: 0x%04X\n", result);
    }
    // Parity should be even
    return (result & 0x0001) == 0;
}
//////////////////////////////////

// Driver Code
void default_shiftRegister() {
    // Parallel output parameters
    stepper_dir = 0;
    stepper_usm1 = 0;
    stepper_usm0 = 0;
    stepper_sleepn = 1;
    stepper_step = 0;
    stepper_resetn = 1;
    stepper_srn = 0;
    stepper_enablen = 0;
    csn_encoder = 1;
    // Latch clock
    csn_shpo = 0;

    data_tx = stepper_dir * pow(2, 0) + stepper_usm1 * pow(2, 1) + stepper_usm0 * pow(2, 2) + 
        stepper_sleepn * pow(2, 3) + stepper_step * pow(2, 4) + stepper_resetn * pow(2, 5) + 
        stepper_srn * pow(2, 6) + stepper_enablen * pow(2, 7) + csn_encoder * pow(2, 9);
    shiftOut(data_tx, &data_rx);
}

void stepper_motion(int direction, int degrees) {
    stepper_dir = direction;
    int num_steps = degrees / 1.8;
    for(int i = 0; i < num_steps; i++) {
        stepper_step = 1;
        data_tx = stepper_dir * pow(2, 0) + stepper_usm1 * pow(2, 1) + stepper_usm0 * pow(2, 2) + 
            stepper_sleepn * pow(2, 3) + stepper_step * pow(2, 4) + stepper_resetn * pow(2, 5) + 
            stepper_srn * pow(2, 6) + stepper_enablen * pow(2, 7) + csn_encoder * pow(2, 9);
        shiftOut(data_tx, &data_rx);

        wait_us(velocity/2);

        stepper_step = 0;
        data_tx = stepper_dir * pow(2, 0) + stepper_usm1 * pow(2, 1) + stepper_usm0 * pow(2, 2) + 
            stepper_sleepn * pow(2, 3) + stepper_step * pow(2, 4) + stepper_resetn * pow(2, 5) + 
            stepper_srn * pow(2, 6) + stepper_enablen * pow(2, 7) + csn_encoder * pow(2, 9);
        shiftOut(data_tx, &data_rx);

        wait_us(velocity/2);
    }
}

void increase_velocity() {
    velocity = velocity - 10;
    printf("Velocity: %d\n", velocity);
}

void decrease_velocity() {
    velocity = velocity + 10;
    printf("Velocity: %d\n", velocity);
}

void stepper_mode(int usm1, int usm0) {
    if(usm1 == 0 && usm0 == 0) {
        stepper_usm1 = usm1;
        stepper_usm0 = usm0;
        printf("Full Step mode is selected\n");
    }
    else if (usm1 == 0 && usm0 == 1) {
        stepper_usm1 = usm1;
        stepper_usm0 = usm0;
        printf("Half Step mode is selected\n");
    }
    else if (usm1 == 1 && usm0 == 0) {
        stepper_usm1 = usm1;
        stepper_usm0 = usm0;
        printf("1/4 Step mode is selected\n");
    }
    else if (usm1 == 1 && usm0 == 1){
        stepper_usm1 = usm1;
        stepper_usm0 = usm0;
        printf("1/8 Step mode is selected\n");
    }
    else {
        stepper_usm1 = 0;
        stepper_usm0 = 0;
        printf("This option is not correct, full step mode is selected\n");
    }
}

void read_angle_encoder() {
    int angle;
    angle = encoder.write(AS_CMD_ANGLE);

    stepper_dir = 0;
    stepper_usm1 = 0;
    stepper_usm0 = 0;
    stepper_sleepn = 1;
    stepper_step = 0;
    stepper_resetn = 1;
    stepper_srn = 0;
    stepper_enablen = 0;
    csn_encoder = 1;

    data_tx = stepper_dir * pow(2, 0) + stepper_usm1 * pow(2, 1) + stepper_usm0 * pow(2, 2) + 
        stepper_sleepn * pow(2, 3) + stepper_step * pow(2, 4) + stepper_resetn * pow(2, 5) + 
        stepper_srn * pow(2, 6) + stepper_enablen * pow(2, 7) + csn_encoder * pow(2, 9);
    shiftOut(data_tx, &data_rx);
    wait_us(1); // Wait at least 350ns after chip select
    
    if( parity_check(angle))
    {
        // Convert range from 0 to 2^14-1 to 0 - 360 degrees
        float deg = degrees(angle);
        printf("Angle: %f degrees\r\n", deg );
    }
    else
    {
        printf("Parity check failed.\r\n");
    }
}

int main() {

    printf("\n\n\n\n");

    char c;

    // SPI Shift Register configuration
    shPo.format(16, 0);
    shPo.frequency(1000000);

    // SPI Encoder configuration
    encoder.format(16, 1);
    encoder.frequency(1000000);

    // Default values at output registers
    default_shiftRegister();

    while(1) {
        
        c = pc.getc();

        switch (c)
        {
            case 'l':
                stepper_motion(1, 90);
                break;
            
            case 'j':
                stepper_motion(0, 90);
                break;

            case 'd':
                stepper_motion(1, 9);
                break;

            case 'a':
                stepper_motion(0, 9);
                break;

            case 'w':
                increase_velocity();
                break;

            case 's':
                decrease_velocity();
                break;

            case 'r':
                default_shiftRegister();
                read_angle_encoder();
                break;
            
            case '1':
                stepper_mode(0, 0);
                break;

            case '2':
                stepper_mode(0, 1);
                break;

            case '3':
                stepper_mode(1, 0);
                break;

            case '4':
                stepper_mode(1, 1);
                break;

            default:
                printf("This option doesn't exist\n");
                break;
        }
    }
}

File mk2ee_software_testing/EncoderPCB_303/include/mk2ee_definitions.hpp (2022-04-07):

#ifndef MK2EE_DEFINITIONS_HPP
#define MK2EE_DEFINITIONS_HPP

#define modifyBitPos(n, p, b) ( ( (n) & ~(1 << (p)) ) | ((b) << (p)) ) // Set or clear a bit given a position
#define setBit(n, p) ( (n) | (1 << (p)) )
#define clearBit(n, p) ( (n) & ~(1 << (p)) )

#define prf_0 (GPIOC -> BSRR) = GPIO_BSRR_BS_3
#define prf_1 (GPIOC -> BSRR) = GPIO_BSRR_BR_3

#define LED1Red     1
#define LED1Green   2
#define LED1Blue    3
#define LED2Blue    4
#define LED2Green   5
#define LED2Red     6
#define SH_PO_CSn   7

#endif

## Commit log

2021-01-26 Fusion 360 project is added
    [MK2 Encoder Enhaced v77.f3z]
2021-01-26 Pieces exported in STL files are added
    [Ball_Bearing_Separator v1.stl, BaseGear.stl, BaseGearBox.stl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]
2021-01-26 KiCAD project is added
    [5024431270.stp, AS5047D-ATSM.stp, ASMB-KTF0-0A306.stp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]
2021-01-27 forward kinematics and stepper motor studies are added
2021-02-09 all components are checked
    [559320210.stp, 559320610.stp, 559350430.stp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]
2021-02-26 PCB design is updated
    [MK2EE.kicad_pcb, driver-1.sch, encoder-1.sch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]
2021-03-02 PCB designs are updated
    [MK2EE.kicad_pcb, driver-1.sch]
2021-03-22 all components are connected
    [MK2EE.kicad_pcb, driver-1.sch, encoder-1.sch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]
2021-05-03 New 3D model of Base part and PCB design is fixed
    [MK2EE.kicad_pcb, driver-1.sch, encoder-1.sch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]
2021-05-03 New 3d modelis updated
    [BaseGearButtom.stl, BaseGearCover.stl, MK2 Encoder Enhaced v77.f3z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]
2021-05-19 PCBs manufacturer options
    [prices_safepcb.ods]
2021-05-19 Thermal pad from stepper driver is modified
    [MK2EE.kicad_pcb]
2021-05-19 Gerber files are added in the project
    [MK2EE-B_CrtYd.gbr, MK2EE-B_Cu.gbr, MK2EE-B_Mask.gbr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]
2021-05-19 Servo testing with PWM
2022-03-28 Software testing for a DriverPCB
2022-03-28 Some changes
    [Aux Support.stl, GearWithCouplerLeft.stl, GearWithCouplerRight.stl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]
2022-03-28 Software testing for EncoderPCB
2022-03-28 Servo PWM: some modifications
2022-03-29 Software testing for EncoderPCB with Nucleo Board F303RE
2022-03-31 Some corrections and documentation
    [main.cpp, mk2ee_definitions.hpp, mySpi.cpp]
2022-04-07 EncoderPCB_303: OOP

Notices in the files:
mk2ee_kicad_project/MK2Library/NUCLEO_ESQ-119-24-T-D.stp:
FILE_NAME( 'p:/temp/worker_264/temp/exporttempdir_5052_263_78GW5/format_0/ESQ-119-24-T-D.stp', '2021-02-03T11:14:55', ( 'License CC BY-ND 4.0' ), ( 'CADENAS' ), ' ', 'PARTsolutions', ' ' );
